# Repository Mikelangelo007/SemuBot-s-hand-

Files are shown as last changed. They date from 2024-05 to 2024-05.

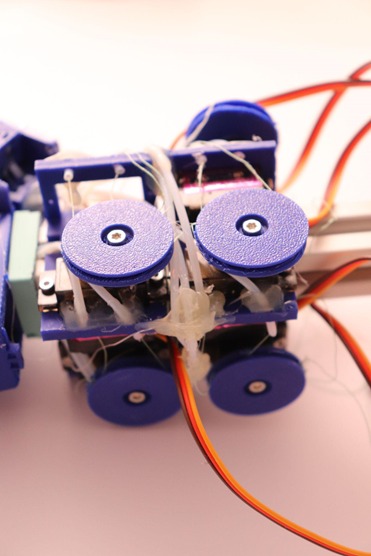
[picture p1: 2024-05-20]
Images/image2 (2).jpeg

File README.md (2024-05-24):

# SemuBot's 3D Printed Hand Assembly

PLA has been used for 3D printing.

### Hand Assembly
- Assembly Hand v18.stl: Hand Assembly

### Thumb Assembly
- Thumb Module v22.stl: Assembly of Thumb
- Thumb Module - Connection to the Palm.stl
- Lower Part Thumb v13.stl: with 3 bearings (2 on sides and 1 on joint to the middle limb)
- Middle Part Thumb v22.stl: with one bearing on joint to the upper limb
- Upper Part Thumb v21.stl

### Other Fingers Assembly

#### Index Finger Assembly
- Stand - others v7.stl
- Lower - Middle Limb 4 - Updated v1.stl x 2
- Upper Limb 1 - Index finger v1.stl

#### Little Finger, Ring Finger, and Middle Finger Assemblies
- Lower - Middle Limb 4 - Updated v1.stl x 2 (for each finger)
- Upper Limb 1 - Little finger - Latest v1.stl (for little finger)
- Upper Limb 1 - Index finger v1.stl (for ring finger if it is a female hand)
- Upper Limb 1 - Index finger v1.stl (for middle finger, but customization is possible)

### Assembly Instructions
- The hand is modular and customizable. Different sizes of finger limbs do not prevent the hand from working, but the connections and holes for the tubes should be properly made and placed.
- In all of the fingers, strings should be fixed to the fingertips from both sides. Strings must go through silicone tubes till the middle of the lower limb. PTFE tubes are connected to the connection module of fingers using hot glue. Then, strings must go through PTFE tubes.
- Palm, Index finger assembly, and "all the fingers connected to the connection module" assembly are assembled as shown in "Assembly Hand v18.stl".
- PTFE tubes must go through the holes inside the palm and exit from the bottom of the palm to the forearm part. Then, the thumb assembly must be connected, and after that, the motor's shell can be assembled. PTFE tubes are glued to the motor's shell, and strings are connected to the same point of motors in "Figure Copy v2.stl".

# Cost Breakdown
| Row | Material | Amount | Cost |
|-----|---|---|---|
| 1 | PLA | 148.26 grams (without supports)| 4 euros |
| 2 | Servo motors with motor gears (MG90S) | 7 | 18.2 euros  |
| 3 | M2 bearing | 18 | - |
| 4 | M2 screw | 19 | - |
| 5 | M2.5 screw | 7 | - |
| 6 | M5 screw | 2 | - |
| 7 | M6 screw | 1 | - |
| 8 | Arduino Nano | 1 | 25 euros |
| 9 | PTFE tube | 2 m | 5 euros |
| 10  | Silicone tube | 2 m | 7.5 euros |
| 11  | Bearings | 19 | 15 euros |
| 12  | 3D printing | - | 10 euros |
| 13  | Assembling | Upmost 2 hours | - |
| 14  | ASA | 2 g | - |
| 15  | **Total** | - | **84.7 euros** |
| 16  | **Working hours** | Upmost 2 hours of Assembly | - |

# Code Scripts - Examples
- Example actuation codes are in the "Servo.py" file.
- For Arduino Nano, the code is in the "sketch_dec16b.ino" file.

Refer to the images "image.png" and "image2 (2).jpeg" for visual guidance.

Author
Elchin Huseynov

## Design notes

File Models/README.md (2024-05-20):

PLA has been used for 3D printing
### Hand Assembly
- Assembly Hand v18.stl: Hand Assembly

### Thumb Assembly
- Thumb Module v22.stl: Assembly of Thumb
- Thumb Module - Connection to the Palm.stl
- Lower Part Thumb v13.stl: with 3 bearings (2 on sides and 1 on joint to the middle limb)
- Middle Part Thumb v22.stl: with one bearing on joint to the upper limb
- Upper Part Thumb v21.stl

### Other Fingers Assembly

#### Index Finger Assembly
- Stand - others v7.stl
- Lower - Middle Limb 4 - Updated v1.stl x 2
- Upper Limb 1 - Index finger v1.stl

#### Little Finger, Ring Finger, and Middle Finger Assemblies
- Lower - Middle Limb 4 - Updated v1.stl x 2 (for each finger)
- Upper Limb 1 - Little finger - Latest v1.stl (for little finger)
- Upper Limb 1 - Index finger v1.stl (for ring finger if it is a female hand)
- Upper Limb 1 - Index finger v1.stl (for middle finger, but customization is possible)

### Assembly Instructions
- The hand is modular and customizable. Different sizes of finger limbs do not prevent the hand from working, but the connections and holes for the tubes should be properly made and placed.
- In all of the fingers, strings should be fixed to the fingertips from both sides. Strings must go through silicone tubes till the middle of the lower limb. PTFE tubes are connected to the connection module of fingers using hot glue. Then, strings must go through PTFE tubes.
- Palm, Index finger assembly, and "all the fingers connected to the connection module" assembly are assembled as shown in "Assembly Hand v18.stl".
- PTFE tubes must go through the holes inside the palm and exit from the bottom of the palm to the forearm part. Then, the thumb assembly must be connected, and after that, the motor's shell can be assembled. PTFE tubes are glued to the motor's shell, and strings are connected to the same point of motors in "Figure Copy v2.stl".

### Cost Breakdown
| Row | Material | Cost |
|-----|---|---|
| 1 | PLA | 4 euros |
| 2 | Servo motors | 18.2 euros|
| 3 | Arduino Nano | 25 euros  |
| 4 | PTFE tube | 5 euros |
| 5 | Silicone tube  | 7.5 euros |
| 6 | Bearings | 15 euros  |
| 7 | 3D printing | 10 euros  |
| 8 | **Total** | **84.7 euros** |
| 9 | **Working hours** | **Upmost 2 hours of Assembly** |

### Examples
- Example actuation codes are in the "Servo.py" file.
- For Arduino Nano, the code is in the "sketch_dec16b.ino" file.

Refer to the images "image.png" and "image2 (2).jpeg" for visual guidance.

Elchin Huseynov

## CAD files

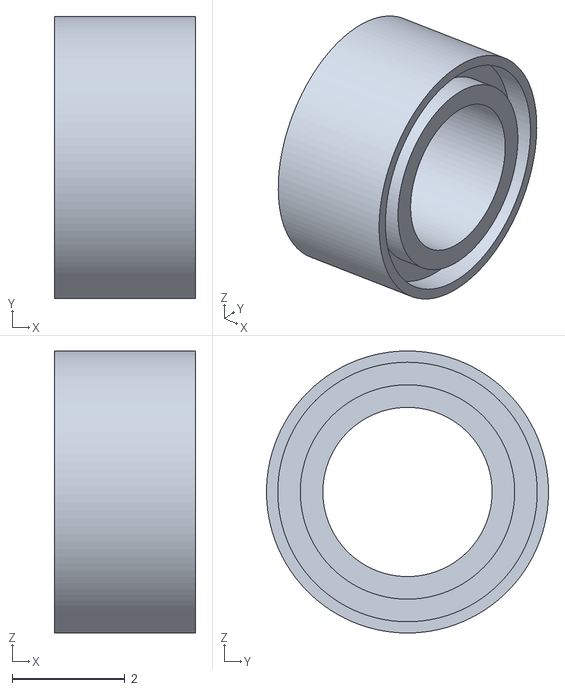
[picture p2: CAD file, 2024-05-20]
Models/Bearing v1.stl
2.50 x 5.00 x 5.00

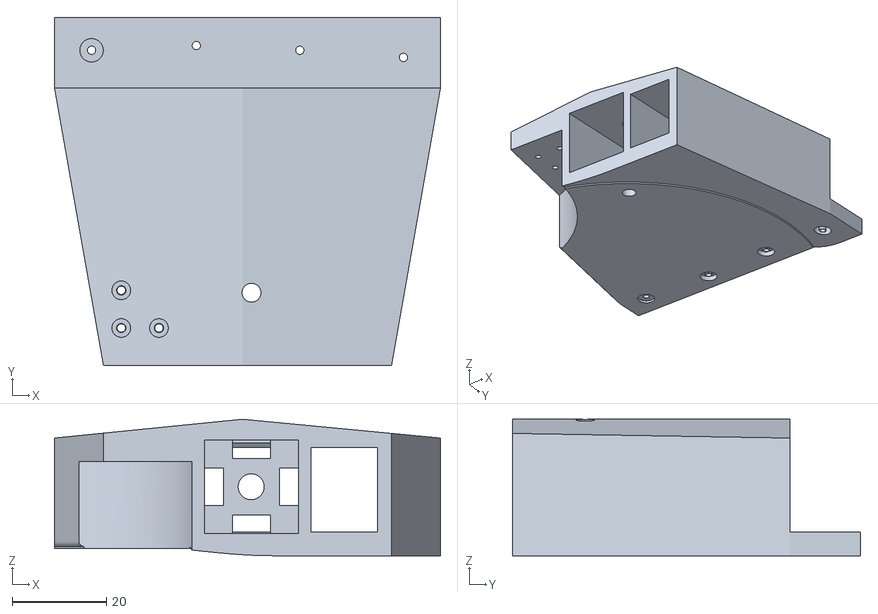
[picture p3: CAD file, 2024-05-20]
Models/Palm.stl
82.0 x 74.0 x 29.0

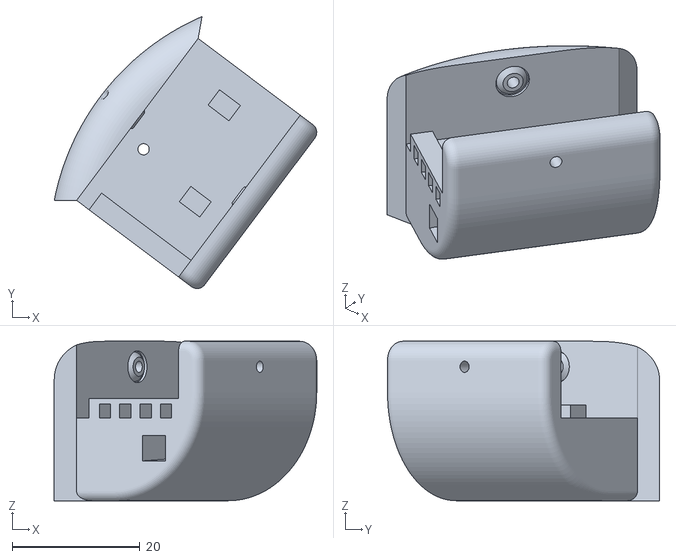
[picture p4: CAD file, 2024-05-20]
Models/Thumb Module - Connection to the Palm.stl
41.1 x 42.6 x 25.0

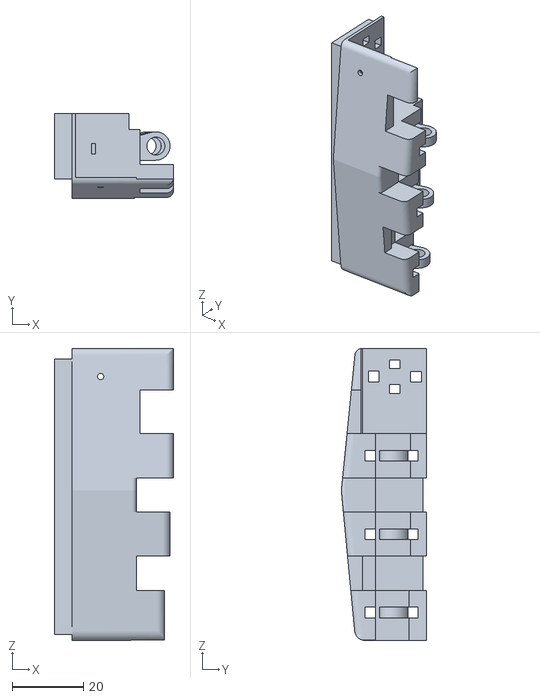
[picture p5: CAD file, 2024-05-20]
Models/Connection Module Fingers.stl
33.5 x 24.0 x 82.0

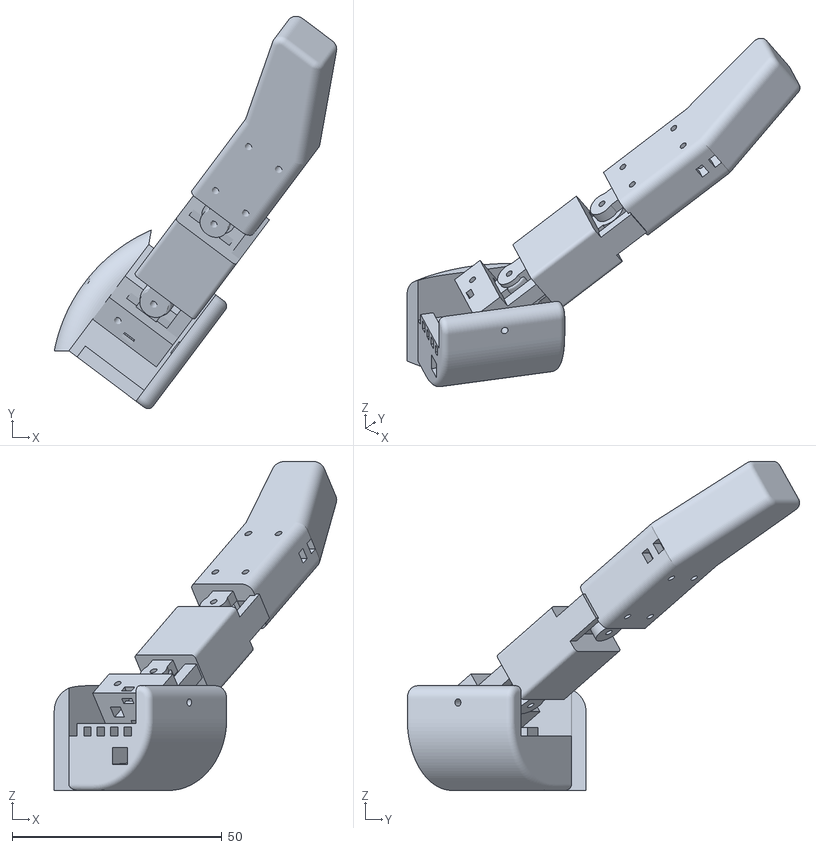
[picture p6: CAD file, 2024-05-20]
Models/Thumb Module v22.stl
67.4 x 93.6 x 78.5

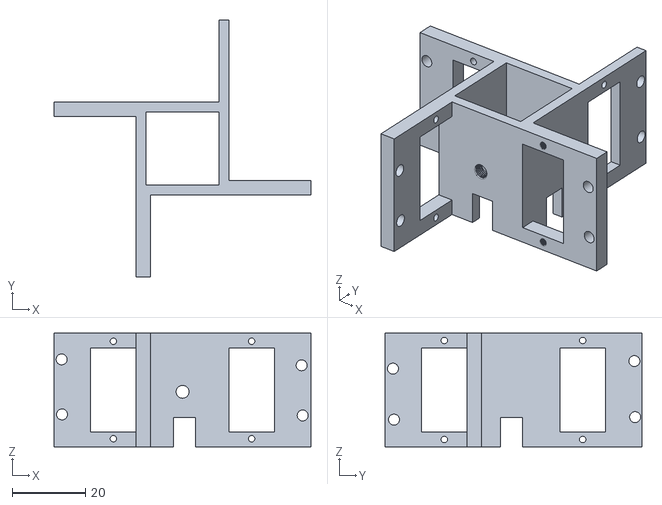
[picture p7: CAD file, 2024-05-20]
Models/Motors Shell v12.stl
70.2 x 70.2 x 31.0

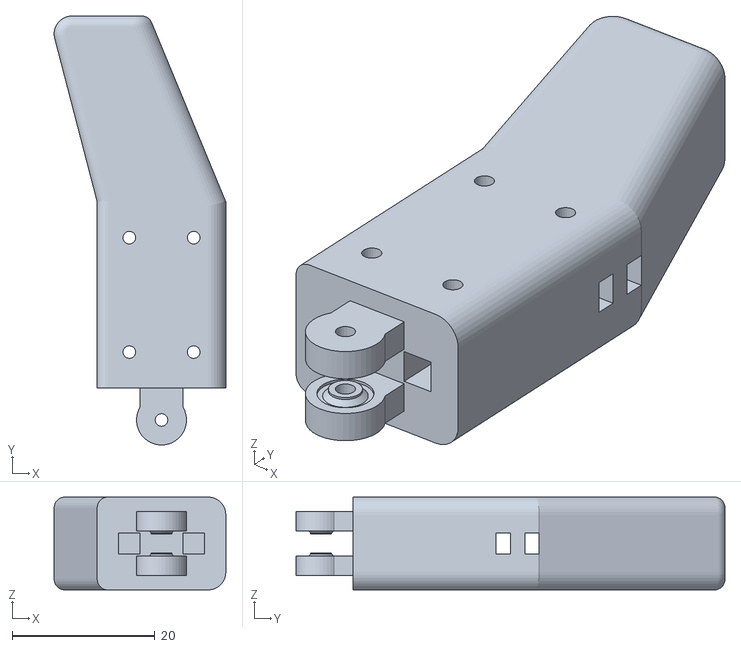
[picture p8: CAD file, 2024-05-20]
Models/Upper Part Thumb v21.stl
24.0 x 60.0 x 13.0

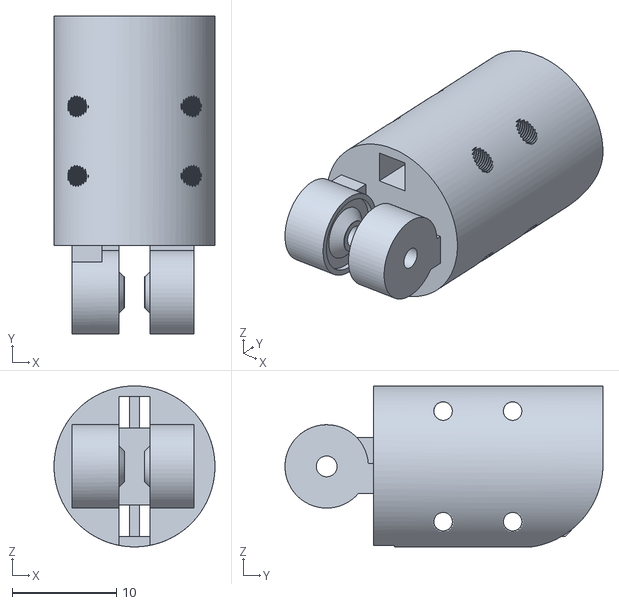
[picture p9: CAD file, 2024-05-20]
Models/Upper Limb 1 - Little finger - Latest v1.stl
15.4 x 30.5 x 15.4

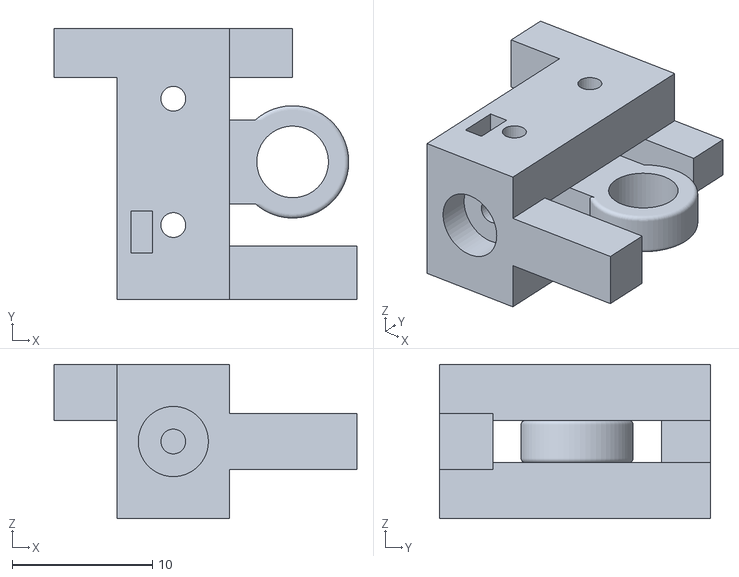
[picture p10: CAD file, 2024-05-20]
Models/Lower Part Thumb v13.stl
21.6 x 19.3 x 11.0

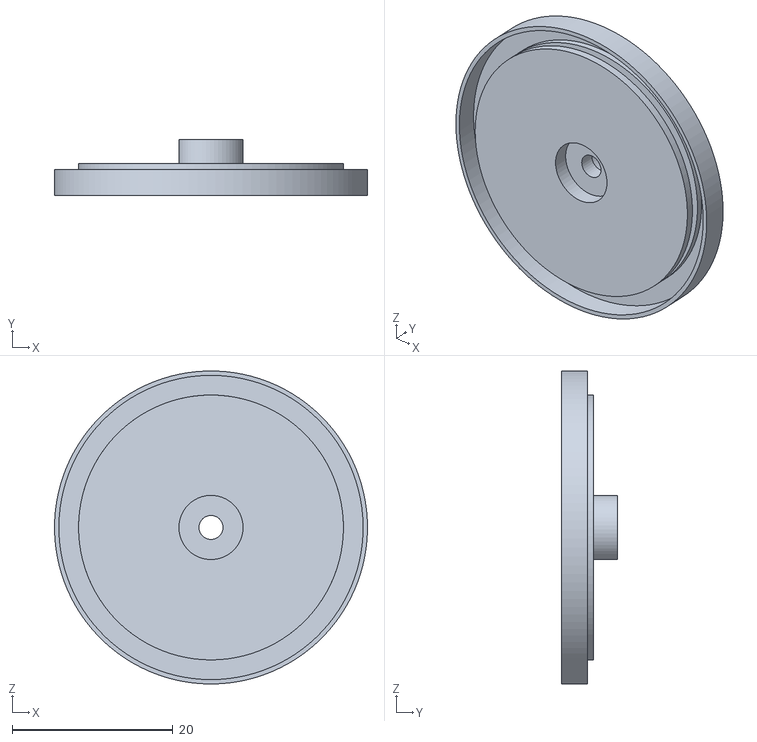
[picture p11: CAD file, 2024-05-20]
Models/Figure Copy v2.stl
39.0 x 7.00 x 39.0

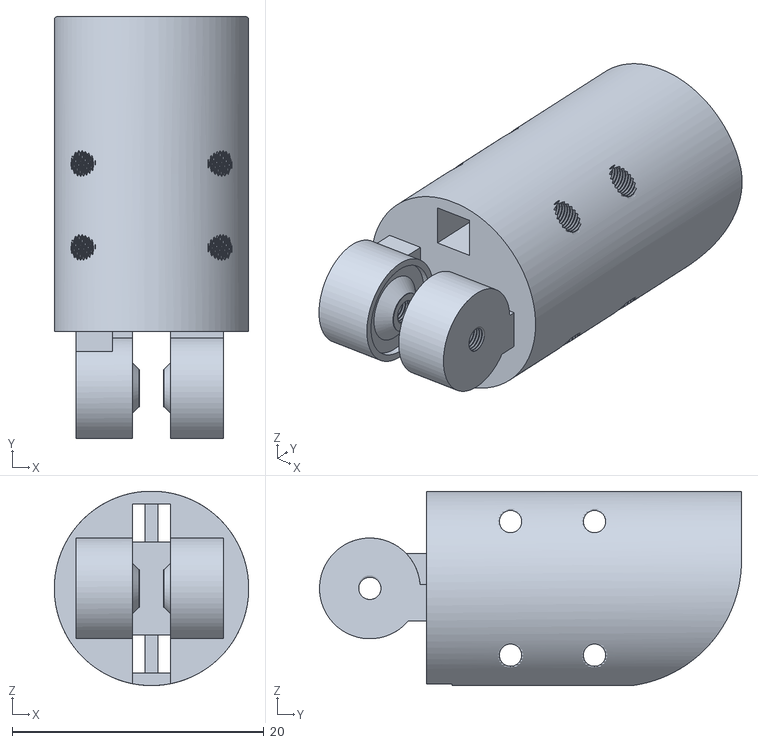
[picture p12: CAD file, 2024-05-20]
Models/Upper Limb 1 - Index finger v1.stl
15.4 x 33.5 x 15.4

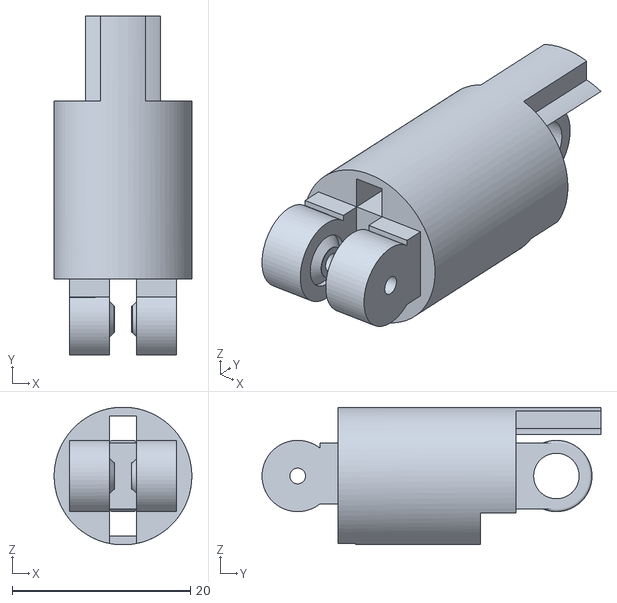
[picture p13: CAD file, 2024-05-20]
Models/Lower - Middle Limb 4 - Updated v1.stl
15.4 x 38.0 x 15.4

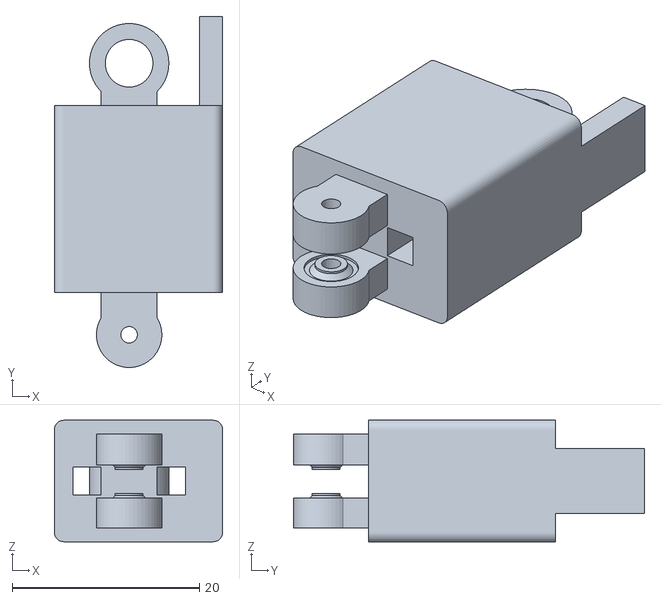
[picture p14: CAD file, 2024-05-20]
Models/Middle Part Thumb v22.stl
18.0 x 37.5 x 13.0

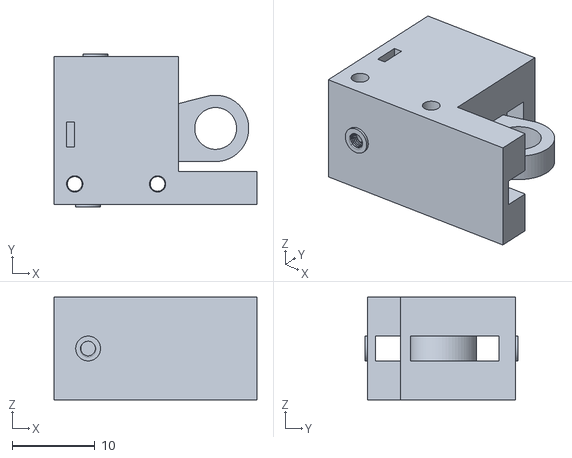
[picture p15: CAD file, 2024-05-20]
Models/Stand - others v7.stl
24.5 x 18.5 x 12.4

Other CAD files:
Models/Palm v47.stl
Models/Thumb Module v1.stl

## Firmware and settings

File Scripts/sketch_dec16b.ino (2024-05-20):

#include <Servo.h>

Servo myservo1;
Servo myservo2;
Servo myservo3;
Servo myservo4;
Servo myservo5;
Servo myservo6;
Servo myservo7;

void setup() {
  Serial.begin(9600);
  myservo1.attach(A2);  // First servo on pin A2
  myservo2.attach(A3);  // Second servo on pin A3
  myservo3.attach(A0);  // Third servo on pin A0
  myservo4.attach(A1);  // Fourth servo on pin A1
  myservo5.attach(A4);  // Fifth servo on pin A4
  myservo6.attach(A5);  // Sixth servo on pin A5
  myservo7.attach(A7);  // Seventh servo on pin A6
}

// Define functions for each servo
void set_servo1_angle(int angle) {
  myservo1.write(angle);
  Serial.println("First servo angle set to: " + String(angle));
}

void set_servo2_angle(int angle) {
  myservo2.write(angle);
  Serial.println("Second servo angle set to: " + String(angle));
}

void set_servo3_angle(int angle) {
  myservo3.write(angle);
  Serial.println("Third servo angle set to: " + String(angle));
}

void set_servo4_angle(int angle) {
  myservo4.write(angle);
  Serial.println("Fourth servo angle set to: " + String(angle));
}

void set_servo5_angle(int angle) {
  myservo5.write(angle);
  Serial.println("Fifth servo angle set to: " + String(angle));
}

void set_servo6_angle(int angle) {
  myservo6.write(angle);
  Serial.println("Sixth servo angle set to: " + String(angle));
}

void set_servo7_angle(int angle) {
  myservo7.write(angle);
  Serial.println("Seventh servo angle set to: " + String(angle));
}

void loop() {
  if (Serial.available() > 0) {
    char command = Serial.read();
    switch(command) {
      case 'a':
        set_servo1_angle(Serial.parseInt());
        break;
      case 'b':
        set_servo2_angle(Serial.parseInt());
        break;
      case 'c':
        set_servo3_angle(Serial.parseInt());
        break;
      case 'd':
        set_servo4_angle(Serial.parseInt());
        break;
      case 'e':
        set_servo5_angle(Serial.parseInt());
        break;
      case 'f':
        set_servo6_angle(Serial.parseInt());
        break;
      case 'g':
        set_servo7_angle(Serial.parseInt());
        break;
    }
  }
}

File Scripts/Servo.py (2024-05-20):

import serial
import time

arduino_port = 'COM5'  # Adjust as necessary
baud_rate = 9600

try:
    ser = serial.Serial(arduino_port, baud_rate, timeout=1)
except serial.SerialException as e:
    print("Error opening serial port:", e)
    exit()

def set_servo_angle(servo_id, angle):
    command = f'{servo_id}{angle}\n'
    ser.write(command.encode('utf-8'))
    time.sleep(0.1)  # Delay for servo movement
try:
    while True:
        
        set_servo_angle('b', 180) # Ring finger close
        time.sleep(2)
        set_servo_angle('b', 0) # Ring finger open
        time.sleep(2)
        # set_servo_angle('a', 0) # index finger close
        # time.sleep(0.8)
        # set_servo_angle('f', 10) # index finger right
        # time.sleep(0.8)
        # set_servo_angle('a', 180) # index finger open
        # time.sleep(0.8)
        # set_servo_angle('c', 180)
        # time.sleep(2)
        # set_servo_angle('c', 0)
        # time.sleep(2)
        # set_servo_angle('d', 180) # Thumb close
        # time.sleep(2)
        # set_servo_angle('d', 0)  # Thumb open
        # time.sleep(2)
        # set_servo_angle('e', 180) # Middle finger close
        # time.sleep(2)
        # set_servo_angle('e', 0) # Middle finger open
        # time.sleep(2)
        
        
        # set_servo_angle('f', 30) #index finger middle
        # time.sleep(0.8)
        
        # set_servo_angle('g', 0)
        # time.sleep(2)
        # set_servo_angle('g', 180)
        # time.sleep(2)
except KeyboardInterrupt:
    print("Program terminated by user.")
finally:
    ser.close()

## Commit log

2024-05-20 STL Files
    [Figure Copy v2.stl, Lower - Middle Limb 4 - Updated v1.stl, Lower Part Thumb v13.stl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]
2024-05-20 Assembly Thumb
    [Thumb Module v22.stl]
2024-05-20 Fake bearing
    [Bearing v1.stl]
2024-05-23 SemuBot's hand first prototype
    [Bearing v1.stl, Connection Module Fingers.stl, Figure Copy v2.stl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]
